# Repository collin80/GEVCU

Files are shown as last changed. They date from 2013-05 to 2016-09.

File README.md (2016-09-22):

GEVCU
=====

Note - If you have pulled this code between July and Sept of 2016 then you received commits that have been
removed from this repo. It has been decided to move development of GEVCU6 code over to the GEVCU6 repo.
If you have the commits from that multi-month window then point your origin to the GEVCU6 repo instead
and everything will still be there and be correct. Sorry for any inconvenience this causes.

Generalized Electric Vehicle Control Unit

Our website can be found at : http://www.gevcu.org

A project to create a fairly Arduino compatible ECU firmware
to interface with various electric vehicle hardware over canbus
(and possibly other comm channels)

The project now builds in the Arduino IDE. So, use it to compile, send the firmware to the Arduino, and monitor serial. It all works very nicely.

The master branch of this project is now switched to support the Due. The master branch is sparsely updated and only when the source tree is in stable shape.

The older Macchina code has been moved to its own branch. This code is now *VERY* old but should work to control a DMOC645.

ArduinoDue branch is more experimental than the master branch and includes the work of Michael Neuweiler.

The WIP branch is sync'd to EVTV's official changes and as such could be considered as a testing ground for the official source code distribution.

You will need the following to have any hope of compiling and running the firmware:
- A GEVCU board. Versions from 2 and up are supported.
- Arduino IDE 1.5.4 - Do not use newer versions of the IDE
- due_can library - There is a repo for this under Collin80
- due_rtc library - Also under Collin80
- due_wire library - once again
- DueTimer library - and again

All libraries belong in %USERPROFILE%\Documents\Arduino\libraries (Windows) or ~/Arduino/libraries (Linux/Mac).
You will need to remove -master or any other postfixes. Your library folders should be named as above.

The canbus is supposed to be terminated on both ends of the bus. If you are testing with a DMOC and GEVCU then you've got two devices, each on opposing ends of the bus. So, both really should be terminated but for really short canbus lines you will probably get away with terminating just one side.

If you are using a custom board then add a terminating resistor. 

If you are using the new prototype shield then it should already be terminated. The DMOC can be terminated by soldering a 120 ohm resistor between the canbus lines. I did this on my DMOC and hid the resistor inside the plug shroud. 

This software is MIT licensed:

Copyright (c) 2014 Collin Kidder, Michael Neuweiler, Charles Galpin, Jack Rickard

Permission is hereby granted, free of charge, to any person obtaining
a copy of this software and associated documentation files (the
"Software"), to deal in the Software without restriction, including
without limitation the rights to use, copy, modify, merge, publish,
distribute, sublicense, and/or sell copies of the Software, and to
permit persons to whom the Software is furnished to do so, subject to
the following conditions:

The above copyright notice and this permission notice shall be included
in all copies or substantial portions of the Software.

THE SOFTWARE IS PROVIDED "AS IS", WITHOUT WARRANTY OF ANY KIND,
EXPRESS OR IMPLIED, INCLUDING BUT NOT LIMITED TO THE WARRANTIES OF
MERCHANTABILITY, FITNESS FOR A PARTICULAR PURPOSE AND NONINFRINGEMENT.
IN NO EVENT SHALL THE AUTHORS OR COPYRIGHT HOLDERS BE LIABLE FOR ANY
CLAIM, DAMAGES OR OTHER LIABILITY, WHETHER IN AN ACTION OF CONTRACT,
TORT OR OTHERWISE, ARISING FROM, OUT OF OR IN CONNECTION WITH THE
SOFTWARE OR THE USE OR OTHER DEALINGS IN THE SOFTWARE.

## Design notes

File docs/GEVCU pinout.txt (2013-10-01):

Pin 1 - +12V Input
Pin 3 - +12V output for first digital input
Pin 7 - EXT GND connection to chassis ground / Battery - (in my case)
Pins 9 & 10 - First canbus
Pin 19 - Gnd connection for first and second analog inputs (Throttle)
Pin 20 - First analog input (Throttle)
Pin 21 - Second analog input (Throttle)
Pin 22 - Third analog input (brake / testing input for me)
Pin 23 - Fourth analog input (test pot on my wires)
Pin 24 - +5V power for first and second analog inputs (Throttle)
Pin 26 - +5V power for third and fourth analog inputs (test pots for me,
probably brake transducer for you)
Pin 30 - Gnd connection for third and fourth analog inputs (Brake / Testing)
Pin 32 - First digital input. Tied to pin 3 above through a switch

I used a gnd at pin 19 for one of the gnds. It really doesn't matter
which one you use. All four (19,29,30,31) are equivalent.

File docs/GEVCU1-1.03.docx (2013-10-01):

GENERALIZED ELECTRIC VEHICLE CONTROL UNIT

GEVCU

SPECIFICATION

Jack Rickard jack@evtv.me

# BACKGROUND

For 40 years and more, individual tinkerers and innovators have been modifying existing automobiles to electric drive and often building electrically powered vehicles from scratch.

The early “controllers” that evolved to replace simple switching and resistive controls to control the speed of the driver motors were mostly pulse width modulated (PWM) devices to provide an averaged DC signal to a series DC motor. These simple chopper voltage control devices were generally referred to as “controllers” and translated driver input from “controls” such as the accelerator pedal, ignition switch, and brake to this motor driving voltage to control its speed and direction – and consequently the vehicle.

There are of course many other types of motors such as separately excited DC motors, brushless DC motors, permanent magnet motors and AC induction motors. Most of these polyphase motors required 3 phase “inverters” to convert the DC power of the battery pack into three phase drive signals varying the voltage and frequency of the power to the motor to accomplish the same thing.

Most of the DC “controllers” received the inputs directly by wiring from the sensors or controls in the cars.

In recent years, among automobile manufacturers, the use of the Controller Area Network bus protocol has been adopted for many of the items in the automobile, including the internal combustion engine – often called an Engine Control Unit or a Vehicle Control Unit which forms the central “brains” of the car. It is connected to various sensors and controls by wire but communicates to other subsystems of the vehicle such as the instrumentation, ABS system, transmission, environmental system using this CANbus as the common link.

Automakers have eschewed the DC motor in favor of either permanent magnet AC motors or AC induction motors. And the “inverters” developed to drive these were interfaced to this same CANbus model for control input.

Because of the varying nature of the cars, the ECU or VCU would be specifically designed for that vehicle. But the Inverters driving AC motors can be somewhat generalized to work in any car by using CANbus to control them.

The VCU would be specifically designed and software specifically written for that vehicle. This was hardcoded into flash memory and defined the operation of the vehicle. No end user input or options were provided. Firmware updates were accomplished by revising the hard code, recompiling, and having the controller reflashed with the new binaries at the dealership during normal maintenance.

And so thousands of these VCUs could be flashed when built, with the software specific to that particular vehicle.

The VCU would of course be completely inappropriate and non functional in another vehicle make or model.

As many automakers are experimenting with product introductions of plug-in electric vehicles and hybrid gasoline/electric vehicles, many of the components used in these vehicles are becoming available when the cars are salvaged and are recycled through salvage yards and such online services as eBay.

As such, they will become a resource to individual tinkerers and those converting existing cars to electric drive.

But almost all of these components were designed to be controlled by the Vehicle Control Unit that came with the original car.

It would be a serious advantage, to have a more generalized vehicle control unit that allowed some basic configuration allowing these conversions to modify operation of the VCU to accommodate THEIR car without the need to entirely rewrite the software and flash the VCU.

As almost all VCU accomplish the same basic functions, a simple configuration input that does not involve assembly language or C programming to change it would be of substantial utility.

This document describes the design of a Generalized Vehicle Control Unit. The multicontroller hardware will allow connection of the basic sensor set necessary to drive the car such as throttle signals, brake signals, ignition signal, and control the basic common outputs such as brake lights, fuel level, rpm, power usage, while serving in the central role of converting these inputs to CAN messages for the inverter to actually drive the car.

The operation of this device can be modified, within fairly narrow constraints, by a simple configuration “menu” style input that non-programmers can access and make changes to, in order to interface the VCU to the particular car they want to convert.

The initial immediate need for this Generalized Vehicle Control Unit was the acquisition of a significant number of Siemens 1PV5135-4WS14-Z motors and Digital Motor Control (DMOC) 645 units from the liquidation of Azure Dynamics Corporation by EVtv.

This DMOC no longer has control inputs, but is rather designed to respond to CANbus commands solely.

The intent in developing this GEVCU, is to not only allow access to a number of OEM hardware components, but also to transfer the product support function faced by the manufacturers and developers of the Inverter Power Electronics to the GEVCU.

In theory, CANbus message digests for ANY motor inverter could be easily patched into the GEVCU to allow operation of that power inverter without ANY support from the developer of the power electronics.

This should quickly allow the developers of power electronics inverters to provide this equipment to individuals at the same or comparable prices as they do to the OEM automakers, without having to incur additional expense to train and support those users in the use of the product. Training and use becomes a function of using the GEVCU itself.

# HARDWARE DESIGN PHILOSOPHY

GEVCU developers can use any hardware they can build or locate that accommodates the basic sensor inputs and instrumentation outputs described in this document. OPEN SOURCE hardware prototype equipment is preferred for GEVCU development and the software should be designed to operate on an open source prototype system. But it is perfectly acceptable to then design custom hardware from that reference design to reduce costs and eliminate extraneous unused components available in the open source prototype system design.

The hardware must provide:

1. At least one CANbus port capable of CAN 1.0 and 2.0b operation, including both 11 bit and 29 bit identifiers.
2. A sufficient number of analog to digital converter inputs of sufficient resolution to accommodate the sensor inputs described in this document. Vehicle sensors are overwhelmingly based on 0-5V architectures. And so these A/D inputs must accept signals in the 0-5v range, and the device must be able to provide 5v supplies to those sensors in sufficient power levels to not alter the 5v reference level when all such sensors are connected.
3. Digital inputs capable of recognizing on/off signals from the vehicle given in 12v and ground states. Active can be either of active high 12v or active low gnd but active high is the normally preferred method as 12v is normally the enabling signal for other systems such as brake lights.
4. Relay driver outputs. Digital outputs suitable for engaging relays, contactors, and other relay like devices in the vehicle.
5. PWM outputs. Sufficient PWM outputs to drive legacy instrumentation such as tachometers and fuel gages as described in this document.
6. ETHERNET port. It is very important for the end user to be able to modify the operation of this device (configure it) without the need for unique external software programs running on specific operating systems. The user should be able to easily configure this device using any device with an Ethernet connection and an http browser. It is actually completely acceptable to also provide means of configuration using a browser via 802.b/g/n wireless, Bluetooth, or Universal Serial Bus (USB) interfaces.

The overall requirement here is that no special type of computer, operation system, or unique configuration software external to the GEVCU can be required to easily modify GEVCU configuration and operation.

Additionally we seek to AVOID the additional expense in the device of a dedicated display and input devices in the GEVCU hardware itself. Once configured, this hardware would be entirely redundant. Configuration is conceivably a one time or perhaps very infrequent event.

7. Processor power sufficient to perform the GEVCU tasks without delay in vehicle operation or control. This is quite important as many systems shut down without regular updated CAN messages to keep them alive and the results of any inability to make schedule could be catastrophic in a moving vehicle.
8. Popularity and user base. When selecting hardware, recognize the advantage of popular and widely adopted devices with large user base. That user base provides a level of additional support and utility that it forms a serious element of the ultimate value of the GEVCU.
9. Tool chain. Strong preference should be given to devices with simple and free compilers such as the Arduino IDE. An open hardware open software device makes little sense if it requires a $2800 compiler environment to make code changes.

# SOFTWARE DESIGN PHILOSOPHY

The basic software design philosophy is to be an open source, object oriented software design. This is to accommodate a couple of needs for the GEVCU

1. Ability to add contributions from any external source or user that prove effective in practice. Anyone should be able to read, modify, recompile and run the original source code to the GEVCU. As such, it should be open source and use inexpensive or free, widely available tool chains to compile. If they are caught in the act of doing something useful, that improvement can be added to the main trunk of the software development.
2. Ability to add support for additional inverters. Almost all of the available inverters accomplish essentially the same functions and provide essentially the same information. But the specific CAN bus IDs, command structure and data formats vary entirely from one inverter to another.

The GEVCU will be initially developed to support the Azure Dynamics DMOC645 inverter. But the ability to add the specific CAN bus message commands for other inverters, without having to make changes to the main program structure in a modular fashion is very important.

Make a strong effort to isolate the inverter object from the rest of the code, with an eye towards allowing the use of other inverter objects with no changes to the non-inverter object code.

3. Object Oriented C++ code is an obvious choice. Assembly language subroutines where desirable or advantageous are perfectly acceptable.
4. Recognize an inevitable desire to add additional functions to this device quite beyond the initial GEVCU spec. The GEVCU, by virtue of it’s central role in vehicle operation, would be the natural place to go for controlling electrically powered air conditioner compressors, CANbus controlled battery chargers, CANbus controlled Electronic Power Assisted Steering units (EPAS) etc.

# COMPLIANCE

For teams developing GEVCU hardware and/or software, it should be noted that compliance with this specification is ENTIRELY voluntary.

That said, there is a slight motivator you might want to take into consideration. I happen to know that software developers are notoriously averse to actually documenting anything and hardware designers are even worse – they not only don’t document but they can’t remember either. They’ll have to get with Charlie and get back to you later.

On the other hand, if you design TO the GEVCU specification, and when making necessary changes NOT in compliance get those changes incorporated BACK into the spec, you will find an odd resemblance between your newly finished product and my upcoming best selling novel :

# INSTALLATION AND OPERATION OF THE GENERALIZED ELECTRIC VEHICLE CONTROL UNIT.

By Jack Rickard.

See the movie at a theatre near you. Coming this summer.

# PART 1 - INPUTS

# THROTTLE

The throttle or accelerator is undoubtedly the central control input for a controller. This is how we vary the power output of the inverter to the motor, and thus motor speed and torque, and consequently vehicle speed.

There are two broad types of throttles that must be accommodated: legacy throttles and modern dual signal drive by wire throttles found in currently manufactured vehicles.

The legacy throttle most widely used is a simple 5kohm potentiometer linked to a mechanical pedal usually by wire. The controller provides 5v and a reference ground to the two ends of the resistor, and the pickup arm of the potentiometer returns some fraction of that source voltage to the controller as the signal input.

There are also single channel hall-effect throttles available on the market. But their operation is largely identical. 5v and ref gnd is provided to them, and they return some value between 0 and 5v based on position.

Modern drive by wire throttles used in vehicles today use the same 5v and ref gnd input, but they will provide TWO signal inputs to the controller. These are often two signals of different scale: ie. 0.5 to 4.5 and 1.2 to 3.2. Or they might be inverse function where one signal is 1-4v while the other is 4-1v. In some cases they can be both differing in scale and direction.

These throttles are generally designed for safety in that the controller is suppose to compare the two signals, which have a known relationship, and if the two signals do not correspond, the assumption is that one or both are faulty. As a result, the controller reduces all motor torque and speed commands to zero. This prevents a runaway situation resulting from loss of ground, or loss of 5v, or other wiring incident or component failure.

PINS: 1. 5vdc supply voltage 50 ma out to sensor

2. Signal 0-5vdc ADC input ADC

3. Optional sanity check voltage ADC input

3. Reference return – ground out to sensor

CONFIGURATION VARIABLES:

THROTMIN: This parameter sets the minimum voltage where the throttle is considered active. Voltages below this value are read as no throttle input.

Example: 0.80 would indicate 0.80v

THROTMAX: This parameter sets the maximum voltage where the throttle is considered active. Voltages above this value are read as no throttle input.

Example: 4.75 would indicate 4.75v

THROTNOTMIN: This parameter sets the minimum voltage where the optional sanity check throttle input is considered active. Voltages below this value are read as no throttle input.

Example: 1.20 would indicate 1.20v

THROTNOTMAX: This parameter sets the maximum voltage where the optional sanity check throttle input is considered active. Voltages above this value are read as no throttle input.

Example: 3.60 would indicate 3.60v

The sanity check is NOT performed if either THROTNOTMIN or THROTNOTMAX is zero. If they are non zero, the percentage of maximum throttle signal between THROTNOTMIN and THROTNOTMAX is calculated. Also the percentage of maximium throttle signal between THROTMIN and THROTMAX is calculated. The two percentages are compared, and if not within 5% of each other, a fault is thrown and CANbus signals generated to put inverter at zero torque and zerospeed.

Note that this calculation MUST handle the case where THROTNOTMIN is a larger positive voltage value than THROTNOTMAX – the inverse case.

THROTREGEN: Voltages between this value and THROTMIN result in a linear increase in regenerative braking, with maximum regenerative braking established by THROTMAXREGEN at the THROTMIN voltage and essentially 0 percent of MAXREGEN at the THROTREGEN point.

Example: 1.50 indicates 1.50v

Zero regenerative braking at 1.50 v increasing to THROTMAXREGEN at THROTMIN.

In this way, as you begin easing off the throttle through the deadband, at THROTREGEN regenerative braking is still zero. As the voltage falls, regenerative braking INCREASES to the point set by THROTMAXREGEN when the voltage falls to THROTMIN. And so the further we remove the throttle, the greater the amount of regenerative torque is applied.

THROTFWD: Typically a small voltage value above THROTREGEN establishing a “dead band” between the THROTREGEN point and the THROTFWD point.

Example: 1.8v

In this example, from THROTREGEN (1.50v_ to THROTFWD (1.8v) is the deadband or coast zone. NO torque or speed commands are provided to the inverter if throttle input is both valid and in this band, allowing the motor and the vehicle to free roll.

The area between THROTFWD and THROTMAX defines the region of forward acceleration with the minimum torque/speed values occurring at THROTFWD and the maximum torque and speed values at THROTMAX.

THROTMAP: This variable represents a voltage between and THROTMAX where a 50% torque and speed level is defined.

A linear increase of torque and speed is mapped between THROTFWD and THROTMAP with 50% of available torque and speed occurring at THROTMAP.

A linear increase in torque and speed is also mapped between THROTMAP and THROT MAX representing the remaining 50% of available torque.

This entered value is then used to warp the throttle curve. For example:

THROTFWD: 1.80v

THROTMAP: 3.80v

THROTMAX: 4.65v

It can be seen that the first 50% of available torque is mapped between 1.80 and 3.80v while the second 50% of available torque is mapped linearly between 3.80v and 4.65v.

In this way, low speed handling and maneuvering has greater resolution spread across 2.00v of the throttle range, while less resolution is provided across the upper 0.85v. Higher resolution is desired at take off, or while parking, or reversing, while it is generally not needed in going from 50% to full power when we are basically just wanting a big increase in power. THROTMAP can be used to slide this point between those two extremes.

THROTMAXREGEN: This variable defines the percentage of available maximum torque that is available for regenerative braking at the THROTMIN point.

Note that a value of 0 indicates no regenerative braking at all using the throttle.

MAXREGEN: This variable defines the percentage of available maximum torque that is ever available for regenerative braking.

MAXTORQ: This defines the maximum torque available for any purpose.

# BRAKE

You might note that the throttle input also has provisions for regenerative braking. The brake signal does as well. We would assume that the vehicle has a fully functional normal brake system, and that it also has a brake switch used to turn on the brake lights.

Regenerative braking is normally a function of the brake input.

PINS: 1. 5vdc supply voltage 50 ma out to sensor

2. Brake pressure sensor signal 0-5vdc input ADC

3. Reference return – ground out to sensor

4. Brake light input – 0 or 12v digital input

CONFIGURATION VARIABLES:

BRAKEMIN: This parameter sets the minimum voltage where the brake sensor is considered active. Voltages below this value are read as no brake input.

BRAKEMAX: The maximum voltage logic will read as valid brake pressure sensor input. Voltages above BRAKEMAX are read as no brake input.

BRAKEMAXREGEN. This is a value from 0 to 100 representing the percentage of MAXTORQ that can be applied during regenerative braking.

The actual value of regenerative braking during a braking event is a linear value between MAXTHROTREGEN at BRAKEMIN and BRAKEMAXREGEN at BRAKE MAX.

In this way, when you remove your foot from the throttle, the regenerative level is set at the value of MAXTHROTREGEN. When your foot first applies to the brake, that SAME level of REGEN is maintained. As more brake pressure is applied, the regenerative braking torque increases until it reaches BRAKEMAXREGEN at the BRAKEMAX point.

Note that by setting BRAKEMAX to some voltage LESS than the actual maximum voltage provided by the sensor, you can slide the regenerative braking zone toward the very lightest application of brake, and as you continue to press the pedal, regenerative braking ceases and the normal brake system takes over. This can be effective to get maxium regenerative braking effect before the normal disk or drum brakes begin to become effective.

Normally, NO regenerative braking will be provided without a secondary signal from the brake light input. This is a secondary input from a separate source used to enable regenerative braking.

BRAKREGENRAMPTIME. This is a value between 0 and 255 representing the number of hundredths of a second to use to ramp from THROTMAXREGEN to BRAKEMAXREGEN if the brake sensor input value is below BRAKEMIN but the brake light input is active.

In this event, we assume we are NOT USING a brake pressure tranducer input at all. But we do have an active brake light switch signal. The regenerative braking will gradually increase from THROTMAXREGEN to BRAKEMAXREGEN in linear fashion across the entered time value with a max time of 2.5seconds.

This is counterintuitive and we’ve actually seen inverters with this function coded in backwards. But it doesn’t work well when braking.

In the event we are not using regen on the throttle, and want to use it on the brakes, but have no transducer, the regenerative braking will gradually be applied when we step on the brake pedal and steadily increase. If we get too much braking, we simply remove our foot from the brake. Regen goes to zero. We can REAPPLY the brake pedal and again regenerative braking starts to increase. In practice, this feels like you are pumping the brakes.

# REGENERATIVE BRAKING ADJUST

Regenerative braking is a highly subjective “feel” issue. It would be very nice to provide a knob on an electric vehicle where the driver could manually adjust the regen level just by turning the knob.

PINS: 1. 5vdc supply voltage 50 ma out to sensor

2. Regenerative brake adjust signal 0-5vdc input ADC

3. Reference return – ground out to sensor

CONFIGURATION VARIABLES:

REGENSCALE. This variable is set between 0 and 100% based on the voltage read on the regenerative braking adjust signal input. Voltages below 1v set this value to 0. Voltages between 1 and 4v are converted to a decimal value less than 1 indicating the percentage of regen desired. Voltages above 4 are read as 4.

THROTMAXREGEN and BRAKEMAXREGEN are scaled by multiplying the values entered on the configuration screen by REGENSCALE.

As a result, potentiometer settings resulting in an input voltage less than 1 effectively disables regenerative braking. Voltages between 1 and 5 scale regenerative braking.

# IGNITION

The switched ignition 12v from the vehicle is used to turn on the GEVCU. It is also the source of power for the GEVCU.

PINS: 1. 12vdc supply voltage in from vehicle ignition switch.

CONFIGURATION VARIABLES: None.

# FORWARD

The internal DIRECTION variable should be used to indicate forward (1), reverse (2), or neutral (0) operation. IF REVERSE and NEUTRAL input pins are inactive, set DIRECTION to 1.

PINS: 1. 12vdc digital input.

CONFIGURATION VARIABLES:

ACTIVEHIGH. This single configuration variable determines if input pins are active high (greater than 4 volts) or active low (less than 3 volts). All digital input pins should be able to endure voltage values up to 15v which may occur in vehicles. This variable applies to ALL digital input pins on the VCU.

# REVERSE

The internal DIRECTION variable should be used to indicate forward (1), reverse (2), or neutral (0) operation. IF FORWARD and NEUTRAL input pins are inactive, set DIRECTION to 2.

PINS: 1. 12vdc digital input.

CONFIGURATION VARIABLES:

ACTIVEHIGH. This single configuration variable determines if input pins are active high (greater than 4 volts) or active low (less than 3 volts). All digital input pins should be able to endure voltage values up to 15v which may occur in vehicles. This variable applies to ALL digital input pins on the VCU.

# NEUTRAL

The internal DIRECTION variable should be used to indicate forward (1), reverse (2), or neutral (0) operation. IF FORWARD and REVERSE input pins are inactive, set DIRECTION to 0.

PINS: 1. 12vdc digital input.

CONFIGURATION VARIABLES:

ACTIVEHIGH. This single configuration variable determines if input pins are active high (greater than 4 volts) or active low (less than 3 volts). All digital input pins should be able to endure voltage values up to 15v which may occur in vehicles. This variable applies to ALL digital input pins on the VCU.

# GENERAL ENABLE

This input can be used to enable the VCU operation. If active, AND the GENERAL DISABLE input is INACTIVE, sets internal variable ENABLE to 1. This internal variable is used to determine whether to allow drive speed and torque commands to the inverter. If this input goes inactive, the ENABLE variable is set to 0.

PINS: 1. 12vdc digital input.

CONFIGURATION VARIABLES:

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

# GENERAL DISABLE

This input can be used to enable the VCU operation. If any of these three input pins go active, sets internal variable ENABLE to 0 regardless of GENERAL ENABLE input. This internal variable is used to determine whether to allow drive speed and torque commands to the inverter. If this input goes inactive, NO change is made to the ENABLE variable and we rely on the general enable input to reset ENABLE to 1.

PINS: 1. 12vdc digital input – DISABLE 1.

2. 12vdc digital input - DISABLE 2

3. 12vdc digital input - DISABLE 3

CONFIGURATION VARIABLES:

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

# LIMP MODE

This input is used to force an immediate reduction in power available via speed and torque command. All speed and torque commands are scaled by the LIMPSCALE variable.

PINS: 1. 12vdc digital input.

CONFIGURATION VARIABLES:

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

LIMPSCALE. 0-100. This configuration variable is used as a multiplier for ALL torque and speed commands to the vehicle. The default value is 100 indicating full power Scotty. Lower values of course reduce output power to the percentage indicated in this variable. The variable is applied ONLY when the LIMPMODE input is active.

# OUTPUTS

# CONTROLLER STATUS

This output is used to indicate status of the GEVCU. If it is turned ON and left on in a steady state, this indicates the GEVCU has powered up, established communications with the inverter, and passed all internal operational checks.

PINS: 1. Digital output LED driver.

CONFIGURATION VARIABLES: None

If this LED is flashed 1 to 9 times, followed by off for two seconds, followed by another series of flashes 1 to 9, this indicates a fault code. Fault codes can be, 11 through 19, 21 through 29, 31 through 39 etc. up to 99.

Fault Code 99 is defined as FAULT - NO FAULT CODE PROVIDED.

Fault Code 11 is defined as NO INVERTER COMMUNICATIONS.

Any developer can register a fault code and we’ll add it. First come, first served.

# PRECHARGE RELAY OUTPUT

This output is used to close a precharge relay, applying high voltage to the Inverter through a precharge resistor. icates the GEVCU has powered up, established communications with the inverter, and passed all internal operational checks.

PINS: 1. Digital output 12v RELAY driver. 500ma

CONFIGURATION VARIABLES:

PRECHARGERELAY: This variable is set by the user using a checkbox or radio button. The variable is set to 1 if selected and 0 if not indicating the need for a precharge relay output on power up.

If 1, a digital output is provided as part of the startup sequence. If the digital output does not provide sufficient current, an external MOSFET may be required to drive the relay.

Many inverters such as Rinehart do their own precharge management. The DMOC 645 does not. So this will always be an optional output configurable by the user.

# CONTACTOR RELAY OUTPUT

This output is used to close a contactor high current relay, applying high voltage to the Inverter directly. Most contactors can experience an initial closing current requirement of up to 1.5 amps and subsequently settle to 300 ma or so.

PINS: 1. Digital output 12v RELAY driver. 1.5 amps.

CONFIGURATION VARIABLES:

CONTACTOR: This variable is set by the user using a checkbox or radio button. The variable is set to 1 if selected and 0 if not indicating the need for a contactor relay output on power up.

If 1, a digital output is provided as part of the startup 3 seconds after the PRECHARGERELAY output. If the digital output does not provide sufficient current, an external MOSFET may be required to drive the contactor.

# REVERSE LIGHT RELAY OUTPUT

This output is used to close a relay, applying 12v to the reverse lights of the vehicle. This will normally be done by the transmission, but on certain vehicles without transmission, could be reversed using the REVERSE input to reverse the motor speed and torque commands. This output is always available and set active whenever the internal DIRECTION variable is set to 0

PINS: 1. Digital output 12v RELAY driver. 500 ma.

CONFIGURATION VARIABLES: None

If the digital output does not provide sufficient current, an external MOSFET may be required to drive the 12v relay

# COOLING RELAY OUTPUT

This output is used to close a relay, applying 12v to drive cooling pumps or fans or both. This is set to active whenever CANbus status signals are received from the inverter indicating a motor or inverter temperature reaching a certain level.

PINS: 1. Digital output 12v RELAY driver. 500 ma.

CONFIGURATION VARIABLES:

COOLINGTEMP: 0-300

This configuration variable allows the user to enter the temperature of either motor or inverter where the coolant output goes active. Zero to 300C.

# MOTOR TEMPERATURE OUTPUT

This is a Pulse Width Modulated output representing motor temperature. It can be used to drive a temperature gage. It will be active only if motor temperature is available from inverter via CAN status message.

PINS: 1. 5v PWM output.

CONFIGURATION VARIABLES:

MOTORMINTEMP: 0-300

This variable allows user to enter a motor temperature corresponding to the lowest reading on their gage and nominally a PWM value of 0%.

MOTORMAXTEMP: 0-300

This variable allows the user to enter a motor temperature in degrees centigrade to correspond with a PWM output of 100%.

# INVERTER TEMPERATURE OUTPUT

This is a Pulse Width Modulated output representing inverter temperature. It can be used to drive a temperature gage. It will be active only if inverter temperature is available from inverter via CAN status message.

PINS: 1. 5v PWM output.

CONFIGURATION VARIABLES:

INVMINTEMP: 0-300

This variable allows user to enter an inverter temperature corresponding to a PWM value of 0%.

INVMAXTEMP: 0-300

This variable allows the user to enter an inverter temperature in degrees centigrade to correspond with a PWM output of 100%.

Output should of course be scaled from INVMINTEMP to INVMAXTEMP 0 to 100%. Temperatures above max will be shown at 100% and temperatures below min will be shown at 0% but of course.

# RPM OUTPUT

This is a pulsed digital output that can be used with a 12v opto isolator to drive a common tachometer. RPM from Inverter CAN status message is converted to a series of digital pulses..

PINS: 1. pulsed digital output.

CONFIGURATION VARIABLES:

TACHPPT:

This variable allows user to enter the number of pulses to output per turn PPT corresponding to their tachometer. The output is scaled to a frequency representing this number of pulses per rpm.

Example: 6000 rpm = 100 rps x 4ppt = 400Hz

# BATTERY CURRENT OUTPUT

This is a pulsed digital output that can be used with a 12v opto isolator to drive a common tachometer. Battery current from Inverter CAN status message is converted to a series of digital pulses..

PINS: 1. pulsed digital output.

CONFIGURATION VARIABLES:

AMPPPT:

This variable allows user to enter the number of pulses to output per turn PPT corresponding to their tachometer. The output is scaled to a frequency representing this number of pulses per rpm.

Example: 600 amp = 100 rps x 4ppt = 400Hz

In this case 600 amps of battery current will appear on a tachometer as 6000 rpm if it is a 4 pulse per turn tachometer.

# OTHER CONFIGURATION VARIABLES

MAX RPM – maximum RPM controller should command to inverter.

MAX TORQUE – maximum torque controller should command to inverter.

MAX REGEN – maximum regenerative braking torque controller should command.

# GEVCU STATUS DISPLAY HTML

### Battery voltage _____v

### Battery current ______A

### Battery power ______kW

### Motor temp: ______C

### Inverter temp: ______ C

### Motor Torque: ______ %

### Motor Speed: ______rpm

### Power used since start: _____kWh

### BUTTON – GEVCU SETUP

# GEVCU CONFIGURATION

# GENERAL LIMITS

### MAXRPM (1000-10000) ______rpm

### MAXTORQUE (0-100): ______%

### ACTIVEHIGH [ ] yes [ ] no

### LIMPSCALE(0-100) ____%

# THROTTLE/ACCELERATOR

### THROTMIN (0.00-5.00v) : _________v

### THROTREGEN (0.00-5.00): _______v

### THROTFWD(0.00-5.00): _______v

### THROTMAP(0.00-5.00): _______v

### THROTMAX(0.00-5.00): _______v

### THROTNOTMIN(0.00-5.00): _______v

### THROTNOTMAX(0.00-5.00): _______v

### 0.00==THROTMIN==THROTREGEN==THROTFWD==THROTMAP=THROTMAX ==5.00

### 0.00==THROTNOTMIN=============================THROTNOTMAX-====5.00

\

# BRAKE INPUT

### BRAKEMIN (0.00-5.00v) : _________v

### BRAKEMAX (0.00-5.00): _______v

# REGENERATIVE BRAKING

### MAXREGEN (0-100): _____%

### REGENSCALE (0-100): _____%

### THROTMAXREGEN (0-100) ____%

### BRAKEMAXREGEN (0-100) ____%

### BRAKEREGENRAMPTIME(0-255): _______seconds

# OUTPUTS

### PRECHARGE RELAY OUTPUT [ ] yes [ ] no

### CONTACTOR OUTPUT [ ] yes [ ] no

### COOLING OUTPUT(0-300): _______centigrade

### MOTORMINTEMP(0-300): _______centigrade

### MOTORMAXTEMP(0-300): _______centigrade

### INVERTERMINTEMP(0-300): _______centigrade

### INVERTERMAXTEMP(0-300): _______centigrade

### TACHPPT (0-8) ____ ppt

### AMPPPT (0-8) ____ ppt

### BUTTON – ACCEPT CONFIG CHANGES

### BUTTON – GEVCU STATUS

# GEVCU CONFIGURATION TOOLTIPS

Tooltips that may be incorporated into GEVCU configuration html form.

# GENERAL LIMITS

### MAXRPM (1000-10000) ______rpm

The maximum motor speed the GEVCU will call for or allow. If this limit is reported by the Inverter, motor torque, speed or both will be reduced by CANbus command.

### MAXTORQUE (0-100): ______%

The maximum motor torque that can be commanded by CANbus

### ACTIVEHIGH [ ] yes [ ] no

Yes indicates activation of digital inputs will be read with 12v applied to pin. No indicates ACTIVE LOW with ground applied to pin read as ACTIVE.

### LIMPSCALE(0-100) ____%

Percent of maximum torque and speed allowed when LIMPMODE input is active.

# THROTTLE/ACCELERATOR

### THROTMIN (0.00-5.00v) : _________v

Values below this voltage are read as a fault on the accelerator input.

### THROTREGEN (0.00-5.00): _______v

Regenerative braking is linearly increased from this voltage/pedal position DOWN to THROTMIN.

### THROTFWD(0.00-5.00): _______v

Region between THROTREGEN and THROTFORWD defines dead band or COAST area of throttle. Torque and speed are linearly increased from this point to THROTMAX.

### THROTMAP(0.00-5.00): _______v

Defines point between THROTFWD and THROTMAX where 50% of available torque/speed is available. By setting this higher, better low speed resolution/control.

### THROTMAX(0.00-5.00): _______v

Voltages above this are read as throttle faults.

### THROTNOTMIN(0.00-5.00): _______v

Minimum voltage of second throttle input. 0 indicates no input. Any other value establishes ratio to THROTMIN

### THROTNOTMAX(0.00-5.00): _______v

Maximum voltage of second throttle input. 0 disables second throttle input. Any other value corresponds to THROTMAX. It is acceptable for THROTNOTMIN to be greater than THROTNOTMAX, indicating a reversed linear input for comparison to the main throttle input.

### 0.00==THROTMIN==THROTREGEN==THROTFWD==THROTMAP=THROTMAX ==5.00

### 0.00==THROTNOTMIN=============================THROTNOTMAX-====5.00

\

# BRAKE INPUT

### BRAKEMIN (0.00-5.00v) : _________v

Voltages below BRAKEMIN are read as brake sensor faults. Regenerative braking is linearly ramped between BRAKEMIN and BRAKEMAX in most instances.

### BRAKEMAX (0.00-5.00): _______v

Voltages above BRAKEMAX are read as brake sensor faults. Regenerative braking is linearly ramped between BRAKEMIN and BRAKEMAX in most instances.

# REGENERATIVE BRAKING

### MAXREGEN (0-100): _____%

Percentage of MAXTORQUE that can be applied as regenerative braking.

### REGENSCALE (0-100): _____%

MAXREGEN, THROTMAXREGEN, and BRAKEMAXREGEN are all reduced identically if this value is less than 100.

### BRAKEMAXREGEN (0-100) ____%a

Percent of MAXREGEN allowed for braking

### BRAKEREGENRAMPTIME(0-255): _______seconds

Number of seconds to ramp from THROTTREGEN to BRAKEMAXREGEN in the event there is no brake pressure sensor input and we are doing regenerative braking from the brake light input only.

# OUTPUTS

### PRECHARGE RELAY OUTPUT [ ] yes [ ] no

Yes if you want a relay drive signal to engage an external relay. No if not.

### CONTACTOR OUTPUT [ ] yes [ ] no

Yes if you want a 1.5amp relay output to engage high voltage contactor relay

### COOLING OUTPUT(0-300): _______centigrade

Temperature of motor or inverter where a COOLING relay output is provided.

### MOTORMINTEMP(0-300): _______centigrade

Minimum motor temperature corresponding to 1% PWM output on MOTOR TEMP output.

### MOTORMAXTEMP(0-300): _______centigrade

Motor temperature corresponding to 99% PWM output on MOTOR TEMP .

### INVERTERMINTEMP(0-300): _______centigrade

Minimum reported inverter temperature corresponding to 1% PWM output on INVERTER TEMP output.

### INVERTERMAXTEMP(0-300): _______centigrade

Inverter temperature corresponding to 99% PWM output on INVERTER TEMP .

### TACHPPT (0-8) ____ ppt

Pulses per turn for dashboard tachometer to read RPM output of GEVCU

### AMPPPT (0-8) ____ ppt

Pulses per turn for dashboard tachometer to read amperes in hundreds on tachometer thousands of RPM gage.

### BUTTON – ACCEPT CONFIG CHANGES

Sends these configuration changes to GEVCU

### BUTTON – STATUS

Causes GEVCU to display current status screen.

# GEVCU EEPROM MAPPING

This section describes the mapping and location of certain configuration variables necessary for the Generalized Vehicle Control Unit. When an end user sends the HTML form containing configuration items, those items will be extracted from the HTML and stored in the Macchina EEPROM so they are persistent between operations. The program can then retrieve these configuration variabales from EEPROM as part of the basic initialization procedure.

1000 unsigned int MAXRPM (1000-10000) ______rpm

1002 byte MAXTORQUE (0-100): ______%

1003 bool ACTIVEHIGH [ ] yes [ ] no

1004 byte LIMPSCALE(0-100) ____%

1005 unsigned int THROTMIN (0-500 /0.00-5.00v) : _________v

1007 unsigned int THROTREGEN 0-500(0.00-5.00): _______v

1009 unsigned int THROTFWD 0-500(0.00-5.00): _______v

1011 unsigned int THROTMAP 0-500(0.00-5.00): _______v

1013 unsigned int THROTMAX 0-500 (0.00-5.00): _______v

1015 unsigned int THROTNOTMIN 0-500(0.00-5.00): _______v

1017 unsigned int THROTNOTMAX0-500(0.00-5.00): _______v

1019 unsigned int BRAKEMIN 0-500(0.00-5.00v) : _________v

1021 unsigned int BRAKEMAX 0-500(0.00-5.00): _______v

1023 byte MAXREGEN (0-100): _____%

1024 byte REGENSCALE (0-100): _____%

1025 byte THROTMAXREGEN (0-100) ____%

1026 byte BRAKEMAXREGEN (0-100) ____%

1027 byte BRAKEREGENRAMPTIME(0-255): _______seconds

1028 bool PRECHARGE RELAY OUTPUT [ ] yes [ ] no

1029 bool CONTACTOR OUTPUT [ ] yes [ ] no

1030 unsigned int COOLING OUTPUT(0-300): _______centigrade

1032 unsigned int MOTORMINTEMP(0-300): _______centigrade

1034 unsigned int MOTORMAXTEMP(0-300): _______centigrade

1036 unsigned int INVERTERMINTEMP(0-300): _______centigrade

1038 unsigned int INVERTERMAXTEMP(0-300): _______centigrade

1040 byte TACHPPT (0-8) ____ ppt

1041 byte AMPPPT (0-8) ____ ppt

GEVCU Specification 1.03 February 7, 2013

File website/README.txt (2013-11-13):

The GEVCU uses the Mini Socket iWifi module from ConnectOne. Documentation can be found at

http://www.connectone.com/?page_id=217

To update the website on the iChip, you have to use their packing tool which is part of their iChipConfig utility and only runs on Windows XP.  If you use Windows 7 you can use Windows XP mode:

http://windows.microsoft.com/en-us/windows7/install-and-use-windows-xp-mode-in-windows-7

Download and install the following:

http://www.connectone.com/wp-content/uploads/2012/06/iChipConfigExternal_2.4.95_setup7.zip

Then to update the website after changes,

1. Launch iChipConfig, click through warnings about not having the com port and limited functionality
2. Choose the "Site Pack" tool
3. Browse to the website/src dir, select the index.htm as default
4. Select "C02128" as the platform and click "Pack". At this point the parameters should show.
5. Select all the parameters, enter 20 for the max length value to fill and click "Fill"
6. Click "Save" and point it to website.img

At this point you upload the image to the GEVCU using http://192.168.3.10/ichip and power cycle the GEVCU to have it activated.

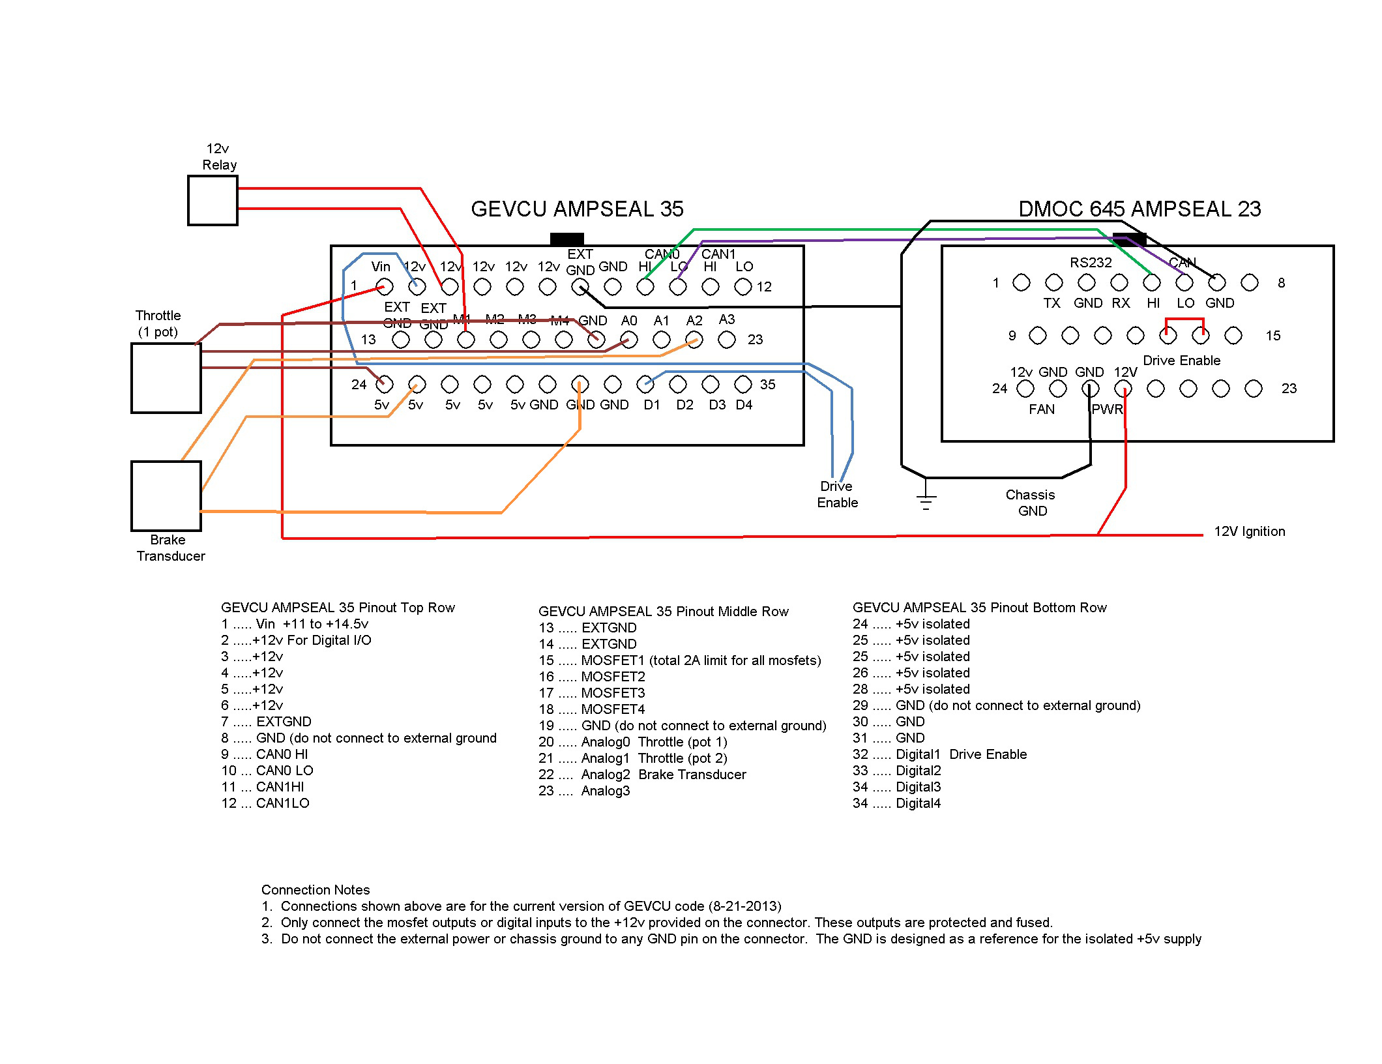
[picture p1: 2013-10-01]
docs/GEVCU-35pinout.jpg

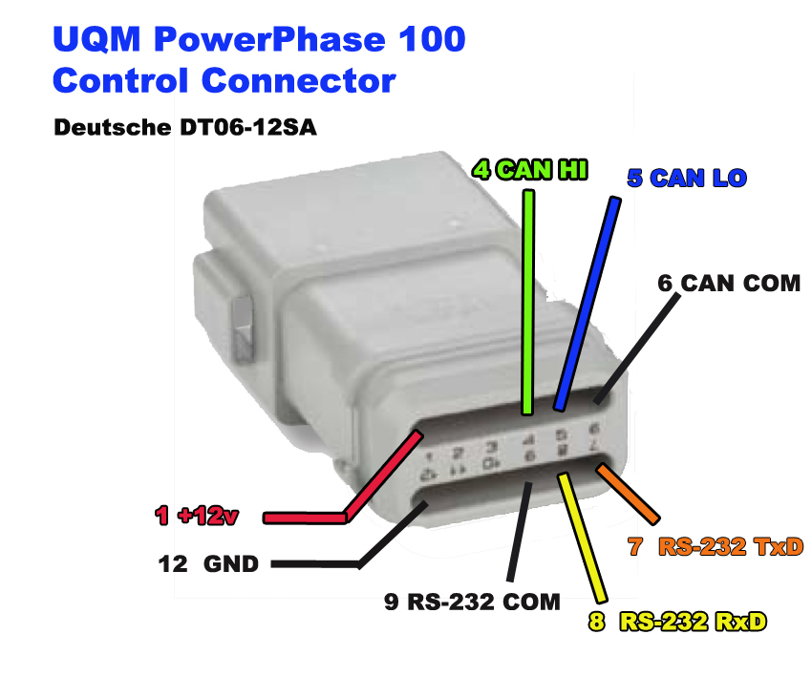
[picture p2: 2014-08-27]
docs/UQMplug.jpg

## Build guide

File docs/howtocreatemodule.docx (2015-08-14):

# GEVCU

Generalized Electric Vehicle Control Unit

# Programmer Checklist

# For Adding Object Modules to the

# GEVCU Software

The Generalized Electric Vehicle Control Unit software is open source and object oriented. It was originally developed to control the Azure Dynamics model 645 Digital Motor Controller (DMOC) – a 3-phase inverter/controller used with the Siemens 1PV5134 motor on the Azure Dynamics eTransit Connect.

The DMOC645 was CAN controlled and did not feature any inputs for throttle, brake or other inputs and outputs. The eTransit Connect Vehicle Control Unit (VCU) performed that duty. Lacking the VCU, we had to develop a VCU from scratch capable of providing the necessary CAN messages to the DMOC645 to in turn control the motor.

The concept of a GENERALIZED VCU specifically for electric vehicles derived from the many different types of cars that would be converted to electric drive using this drive system. But from the beginning we saw the need to drive other types of controller/inverters and indeed interact with other devices such as chargers, DC-DC converters, and battery management systems.

So a central tenet of the GEVCU was a very object oriented approach that would easily allow the addition of new classes and new objects to accommodate different equipment. The goal of course to limit software changes to just the additional object added to accommodate the new equipment.

Some wins and some losses. Indeed GEVCU now supports the BRUSA drive train, the CODA/UQM drive train, and more are envisioned and already a series of chargers, BMS, and other devices have been added.

But along the way, we encountered several targets of opportunity that were just two good to pass on, that tend to complicate the easy addition of object modules.

CREATE OBJECT MODULE

TASKING AND PRIORITIES.

PERSISTENT CONFIGURATION STORAGE

MULTIPLE DEVICES ON CAN

# CREATING AN OBJECT MODULE

You create an object module basically by adding a .cpp and .h file to the program set defining your object module. The best way is to copy one from a similar device. If you are doing an object module for a motor controller, a good start would be to copy and rename the DMOC645 motor controller object module held in DmocMotorController.cpp and DmocMotorController.h

Let’s call the new module EVIC and we’ll rename the copied files EVIC.cpp and EVIC.h.

To add these to the program, you basically do two things.

1. Add an include for EVIC.h in the GEVCU.h header file.

#include "EVIC.h"

2. Add a createObjects entry in the main program file GEVCU.ino

void createObjects() {

PotThrottle *paccelerator = new PotThrottle();

CanThrottle *caccelerator = new CanThrottle();

PotBrake *pbrake = new PotBrake();

CanBrake *cbrake = new CanBrake();

DmocMotorController *dmotorController = new DmocMotorController();

CodaMotorController *cmotorController = new CodaMotorController();

DCDCController *dcdcController = new DCDCController();

BrusaMotorController *bmotorController = new BrusaMotorController();

ThinkBatteryManager *BMS = new ThinkBatteryManager();

ELM327Emu *emu = new ELM327Emu();

ICHIPWIFI *iChip = new ICHIPWIFI();

EVIC *eVIC = new EVIC();}

Here, we instantiated the object eVIC of type EVIC as a new instance of EVIC().

Our eVIC object is now part of the program and enjoys all the rights and privileges of other objects of the program.

Note that most objects you will create will actually be child objects of more generalized parent objects. A motor controller object, for example, usually inherits from MotorController and from CanHandler. Much of the basic work common to all motor controllers is already done for you in the parent and standard variables are already there for you to update from your own specific code. You also generally must inherit from CanHandler to be able to catch and send CAN messages in your object.

So you will find something like this in your .h file.

class EVIC: public Device, CanObserver {

public:

Here, in EVIC.h, we are defining a new class EVIC which inherits from the generic Device class but also from CanObserver. A motor controller might be better to inherit from MotorController and CanObserver.

Obviously, you will likely have to rename almost all the class references in your .cpp and .h files.

# TASKING AND PRIORITIES

We hesitate to claim we have duplicated Linux and a real time operating system here. But the Arduino Due does sport an interesting set of clocks – 3 of them actually – each with 3 configurable interrupt timers for a total of 9 timer interrupts.

Inverter/controllers are operating powerful motors in real time and can be a bit demanding in that they want constant attention – regularly updated CAN control messages or they tend to shut down as a safety consideration. So inverters need the highest priority.

GEVCU does provide information to the user and allows configuration either by USB serial port or via a wireless web site. But while driving down the road, it would be quite normal for NO ONE to be using this at all to configure the system. So this is an example of a very low priority. Chargers and Battery Monitors and so forth would fall somewhere in between.

So we have developed a module called a TICK HANDLER. Your object module must register with this TICK HANDLER and then provide a public method, also termed TICKHANDLER to perform its duties as it can when the TICKHANDLER passes it a tick (timeslice).

You can think of your tickhandler as the LOOP routine in the Arduino Sketch/Processing environment or more traditionally MAIN.

To register your object with the tickhandler, the following general steps are in order.

1. Add a tickhandler DEFINE for your object to config.h file to set your tick interval in microseconds.

#define CFG_TICK_INTERVAL_EVIC 100000

Here, we define a tick interval for EVIC to call it every 100,000 microseconds (100 milliseconds)

2. Add a setup function to your object module establishing tickhandler

void EVIC::setup()

{

TickHandler::getInstance()->detach(this);//Turn off tickhandler

(Any number of other setup statements)

TickHandler::getInstance()->attach(this, , CFG_TICK_INTERVAL_EVIC);

}

In case our tickhandler is on, we turn it off. Perform any other setup functions desired. And then attach the tickhandler using the DEFINE from config.h.

3. Add a tickhandler function to your object module

void EVIC::handleTick()

{

sendCmdCurtis();

sendCmdOrion();

}

Here, we have a short function that calls two other functions. Each of those create and send a CAN command. So each 100 ms, the tickhandler will call the object function handleTick, which will send two CAN messages and return.

4. In your object module .h file, add the following includes:

#include "config.h"

#include "TickHandler.h"

# PERSISTENT CONFIGURATION STORAGE

Almost all modules in the GEVCU have some level of need to store information between operating sessions. This may be system data that you want to maintain from startup to startup such as accumulated Ampere-Hours or peak temperatures.

But almost all devices have some configuration options that end users can adjust to modify the operation of the software.

The Arduino Due ARM3 processor gives us very good power and speed for the VCU function, but it does not provide an EEPROM and the use of flash memory for persistent data has a problem in that it is totally erased if the software is updated.

So GEVCU has a 2Megabit (256kbytes) EEPROM provided just for such persistent data.

In coding independent objects that could be enabled in a variety of combinations, we have to have some means of rationalizing who stores what at what address and when. Otherwise, objects would be overwriting each other’s data.

Further, EEPROM’s have a defined write life. Not quite the issue it was originally, it is still nice to limit the number of writes so that the same data is not rewritten every 30 msec.

We do this with a device termed a MEMCACHE. An object has to register with DEVICES and is allocated a block of memory in MEMCACHE. The data in MEMCACHE is then recorded to EEPROM periodically. And it is loaded into MEMCACHE on startup. In this way, you can save your configuration data and load it again on the next startup.

1. Each device should create a configuration class that inherits from DeviceConfiguration. This will be in your .h file.

class EVICConfiguration: public DeviceConfiguration {

public:

};

2. The loadConfiguration() and saveConfiguration() methods of DmocMotorController and MotorController can be used as a reference for how to load and save configurations.
3. PrefHandler handles the memcache for various devices. Each device needs its own unique name and id number. These are held in the file DeviceTypes.h

enum DeviceId { //unique device ID for every piece of hardware possible

DMOC645 = 0x1000,

BRUSA_DMC5 = 0x1001,

CODAUQM = 0x1002,

BRUSACHARGE = 0x1010,

TCCHCHARGE = 0x1011,

LEAR=0x1012,

THROTTLE = 0x1030,

POTACCELPEDAL = 0x1031,

POTBRAKEPEDAL = 0x1032,

CANACCELPEDAL = 0x1033,

CANBRAKEPEDAL = 0x1034,

EVICTUS = 0x4400,

ICHIP2128 = 0x1040,

DCDC = 0x1050,

THINKBMS = 0x2000,

SYSTEM = 0x5000,

HEARTBEAT = 0x5001,

MEMCACHE = 0x5002,

PIDLISTENER = 0x6000,

ELM327EMU = 0x650,

INVALID = 0xFFFF

};

Here, for the EVIC class we call the device EVICTUS and assign the number 0x4400 to it.

In our object file EVIC.cpp, we have to alter our device constructor to include this.

EVIC::EVIC() : Device()

{

prefsHandler = new PrefHandler(EVICTUS);

commonName = "Andromeda Interfaces EVIC Display";

}

This registers us for the PrefsHandler to provide memcache space. We can then use LoadConfiguration and SaveConfiguration to handle our persistent data that we want to use from session to session without loss.

# MULTIPLE DEVICES ON CAN

GEVCU provides two independent CAN ports that can be configured for different speeds and operated more or less simultaneously. The nature of CAN is that a variety of hardware devices can be on the bus simultaneously as long as they all use the same data speed. And so of course a variety of object modules is envisioned, each servicing one or more CAN devices.

Again to accommodate this without chaos, we have developed a CAN handler. The CAN handler monitors the two CAN busses and when a CAN message is received, the message is passed to the appropriate module. And so each module performing CAN tasks must be registered with the CAN handler as to which specific CAN message IDs it wants to receive.

A canbus handler allows your device to register to receive frames that match the mask. The call to attach has four parameters. The first will basically always be “this”. The second is the ID to match, the third is the mask, and the fourth specifies whether you are interested in standard (false) or extended (true) frames.

canHandlerEv->attach(this, 0x230, 0x7f0, false);

canHandlerCar->attach(this, 0x650, 0x7f0, false);

In this case, we are registering with CAN bus 0 (Ev) to receive any message with an id between 0x230 and 0x23F.

We are also registering with CAN bus 1 (Car) to receive any CAN message with ID 0x650 through 0x65F.

If you need a quick refresher on masks and IDs: CAN bus filtering happens by taking every incoming frame and doing a bitwise AND with each registered mask in turn. The result of this is then compared to the associated ID for that mask. If the two match then your device will receive that frame. For instance, if a frame with 0x23D were to come in and the DmocMotorController had registered a mask of 0x7F0 and an ID of 0x230. 0x23D AND 0x7F0 = 0x230. This does match the ID and so DmocMotorController would get the frame.

Your class should have a handleCanFrame() method if you have registered one or more canbus handlers. This method takes a pointer to a CAN_FRAME structure as input.

# void DmocMotorController::handleCanFrame(CAN_FRAME *frame)

{

}

To send a frame, first create a CAN_FRAME structure variable, fill it out, and use sendFrame() to send it.

### CAN_FRAME output; //establishes variable output of structure CAN_FRAME

### output.length = 8; //Sets number of bytes in payload

### output.id = 0x207; //Sets message id

### output.extended = 0; //0 standard 11 bit frame 1 for extended 29bit frame

### output.data.bytes[0] = 0xa5; //This is simply puts value 5A

### output.data.bytes[1] = 0xa5; //in the first three payload bytes

### output.data.bytes[2] = 0x5a;

### output.data.bytes[3] = 0x00;

### output.data.bytes[4] = 0x00;

### output.data.bytes[5] = 0x00;

### output.data.bytes[6] = 0x00;

### output.data.bytes[7] = 0x00;

### CanHandler::getInstanceEV()->sendFrame(output); //Send the frame

IN this case we establish the variable output as type CAN_FRAME

We set the length to 8 bytes and the message ID to 0x207. We set it for standard 11bit frames and then populate the eight bytes with whatever we like. Then call the can handler to send frame OUTPUT. On the EV (CAN0) bus.

So note that we used a call to the can handler to register our ids and masks for incoming messages, and provided a method to handle those incoming messages by the specific name handleCanFrame.

We used another call to the canhandler to send a message we had preloaded into a CAN_FRAME variable.

In this way, all traffic is handled by the can handler and it can intelligently parse out CAN frames to hungry object modules waiting for them , and also stream messages onto the bus without collision or panic party.

The GEVCU project is designed such that the core system can be extended with modules that provide support for various pieces of hardware. Designing a new module is not conceptually complex but does require several things to be successful.

Note about formatting: BOLD words are class names. Italic words are file names. Underlined words are methods or members of a class. Methods are postfixed with ().

1. The first order of business is to find an existing module of hopefully the same basic type as your desired new module. For instance, if you hope to add support for an XYZ inverter then maybe you’d like to copy the DmocMotorController class. Rename the files with the same format. Maybe you’d name the files XYZMotorController.cpp and XYZMotorController.h If you cannot find an existing device of the same type then still use an existing set of files. The DmocMotorController class could be used as the basis for most any other device.
2. Rename all of the class references in the copied files as well.
3. Notice that DmocMotorController inherits from MotorController and CanObserver. If you are not creating a motor controller class then inherit from something else. Currently the other good choices are Throttle or Device. Device is always a decent choice if no more specific parent class exists. Inheriting from CanObserver is required if your device needs access to either of the CAN busses.
4. Each device can store data within EEPROM. Each device should create a configuration class that inherits from DeviceConfiguration. The loadConfiguration() and saveConfiguration() methods of DmocMotorController and MotorController can be used as a reference for how to load and save configurations.
5. Each device also must have a unique ID and should set what type of device it is. These are set with getId() and getType(). There is a global list of IDs that you should add your device to. DeviceTypes.h contains both the allowable device types and the ID of each and every device that is compiled into the firmware. You will note that DmocMotorController does not contain getType(). Instead it maintains the parent class version since it is still a motor controller.
6. Next, edit the constructor. Most of the constructor will be custom to your device but you will need to set prefsHandler to use your device ID constant instead of DMOC645. Also, set commonName to a nice, short description of your device.
7. Then there are several edits to make in the setup method. As shown in the DmocMotorController class, one should set up the tick handler, load the EEPROM configuration, call the parent setup (if applicable), and set up canbus handlers (if applicable).
  a. A tick handler allows your device to receive periodic ticks so that it can do processing at set intervals. This might be so that you can send canbus frames or so that you can check for input on one or more pins.
  b. Your class should have a handleTick() method if you have registered a tick handler.
  c. A canbus handler, handleCanFrame(), allows your device to register to receive frames that match the mask. The call to attach has four parameters. The first will basically always be “this”. The second is the ID to match, the third is the mask, and the fourth specifies whether you are interested in standard (false) or extended (true) frames. If you need a quick refresher on masks and IDs: Canbus filtering happens by taking every incoming frame and doing a bitwise AND with each registered mask in turn. The result of this is then compared to the associated ID for that mask. If the two match then your device will receive that frame. For instance, if a frame with 0x23D were to come in and the DmocMotorController had registered a mask of 0x7F0 and an ID of 0x230. 0x23D AND 0x7F0 = 0x230. This does match the ID and so DmocMotorController would get the frame.
  d. Your class should have a handleCanFrame() method if you have registered one or more canbus handlers. This method takes a pointer to a canbus frame as input.
8. As covered above, handleTick() and handleCanFrame() will form the majority of the action in most devices. Many devices will want to be able to send canbus frames out as well. This is done through CanHandler::getInstanceEV() or CanHandler::getInstanceCar(). The MotorController class pre-caches CanHandler::getInstanceEV() into the canHandlerEv member. To send a frame, first create a CAN_FRAME variable, fill it out, and use sendFrame() to send it. The DMOC sendCmd1 method shows how to do this.
9. If your device handler needs access to physical IO then use the systemIO member variable inherent to all devices. This variable references the SystemIO class which has the ability to interact with all of the digital I/O and analog inputs.
10. Now that the device handler has been constructed it is time to connect it with the rest of the system. In GEVCU.ino there is a function called createObjects(). You will need to instantiate your class here. You will also have you add your .h file as an include in GEVCU.h. With this done everything should automatically work. The system uses the PrefsHandler instance you setup in the class constructor to determine whether a given device is enabled and only sets up devices which are enabled.
11. A consequence of above is that you *must* enable your new device before it will do anything. This is done by typing “ENABLE=” followed by the ID of your new device.
1. Create your object.cpp and object.h files for your class. Often it is of help to copy an existing file set and rename them. If your new object is a motorcontroller, for example, use dmocMotorController.cpp and dmocMotorController.h. If it is a charger, copy a charger module.
2. List your device in DeviceTypes.h
3. Add your device as an include in GEVCU.h
4. Revise the createObjects section of GEVCU.ino to instantiate your class there.

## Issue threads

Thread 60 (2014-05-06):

Problems with 1.5.6 Arduino IDE

collin80, 2014-05-06:
The firmware seems to experience random hard freezes if compiled under 1.5.6. As such, don't try to do that right now until the problem is corrected either on our end or Arduino's end.

collin80, 2015-03-15:
Everything seems to work properly in 1.6.0 so don't use 1.5.7 and instead upgrade to 1.6.0 which is the new stable version of the IDE.

Closed 2015-03-15.

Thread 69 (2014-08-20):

Torque slew rate is slow

collin80, 2014-08-20:
This issue could be either in the GEVCU code or in the DMOC or both. When you step on the throttle it doesn't quite respond with the proper haste. There is a lot of throttle smoothing going on on the GEVCU side so that might be the cause or the DMOC might be limiting torque slew rate. This should be investigated and solved one way or the other.

neuweiler, 2017-04-01:
unless you've integrated my code which artificially adds "slew" to the throttle, the response of the throttle class itself is immediate. It might be that analog inputs add some slew. With a CAN bus throttle and Brusa motor controller, the repsonse is immediate. (that's why I added a slew rate in the ArduinoDue branch)

collin80, 2017-04-02:
Yes, subsequent to creating this issue we then got the UQM inverter working. It works perfectly fine. It appears that the issue was solely with the DMOC inverter. It apparently has a torque slew rate setting that needs to be changed. This isn't a GEVCU issue. Closing.

Isaac96, 2019-06-09:
Any recollection on what torque slew rate setting you adjusted in the DMOC? Also, it seems like there's a hard limit on the amps we can draw, or perhaps that's a function of other settings? (Trying to decide if we should replace the controller board on the DMOC with Johannes Huebner's open inverter, but first want to max out the DMOC 645.) Thanks!

collin80, 2019-06-09:
I don't remember. It has been years since I actually used a DMOC in a car. I have a DMOC "on the bench" if by that I mean "it's kind of hooked up in a heap under a shelf." I will try to connect to that DMOC this week and see if I can find the setting.

Isaac96, 2019-06-11:
Thanks Collin. My son (and this is his gihub account I'm writing to you on) has gone through all of your GEVCU code while building our car, and has used your CAN library on several arduinos to control various things like a Leaf BMS and Volt DC-DC. Thanks for the great code!

Isaac96, 2019-06-21:
Collin I wonder if you could send us your par file?

Closed 2017-04-02.

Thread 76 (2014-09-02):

Merge good stuff from ArduinoDue branch into WIP branch

collin80, 2014-09-02:
The official EVTV branch is now based on the WIP branch and not the ArduinoDue branch. However, there were valuable commits to the ArduinoDue branch that should be backported to the WIP branch. So, this will now commence. The inverse should also happen - porting relevant changes to WIP into the ArduinoDue branch. There are some philosophical differences between the two branches but the majority of the code is the same.

collin80, 2015-03-15:
I did end up merging a couple of things back into the main code. That happened some time ago. So, this will be closed now.

Closed 2015-03-15.

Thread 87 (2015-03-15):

Investigate serial buffering between MCU and IChip

collin80, 2015-03-15:
Arduino 1.6.0 includes new code to implement serial TX interrupts. This allows serial writing to be non-blocking most of the time. However, no one knows for sure how this has affected the ichip interface code. Are we filling up the TX buffer? How often does it block if so? Can some of the complications in the ichip param updating code be removed now?

collin80, 2015-03-16:
Is it possible to stop sending updates to the web interface if we know that nobody is listening? Perhaps a 10 minute time out? Can we figure out if anyone is listening?

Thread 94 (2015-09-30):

Outputs trigger on start up

collin80, 2015-09-30:
All outputs trigger for a short time on start up. They soon go to proper state

collin80, 2015-11-18:
This a hardware issue where there isn't a pull down on mosfets so they float active for a moment upon start up. Can be fixed by adding pull downs between the MCU pins and the mosfet driver chips. There is no software fix.

collin80, 2017-04-02:
Was fixed in GEVCU6 by adding the appropriate pull downs. There isn't anything to be done for earlier GEVCU versions so I suppose I should just close this now.

Closed 2017-04-02.

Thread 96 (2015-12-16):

PWM outputs

collin80, 2015-12-16:
GEVCU5 boards are capable of PWM on the outputs but there is currently no support for this functionality in software. It would be nice if it were possible to set up a PWM map on the GUI interface that allows the end user to calibrate the PWM output to how their gauge works.

jrickard, 2015-12-16:
The PWM output has a problem I think.  Maybe I'm wrong.  Get me
straightened out.  With this low side switching isn't ON off and OFF is on
and so forth?  So no output is a solid 12v and as we increase the pulse
width the PWM output would go DOWN instead of up.  This is a little
counterintuitive.

Jack Rickard

On Tue, Dec 15, 2015 at 8:44 PM, Collin Kidder <notifications@github.com>
wrote:

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

--
http://www.EVTV.me <http://EVTV.me>

Electric Vehicle Television - KickinGas  - One Car at a Time.

jrickard, 2015-12-16:
You should have a truckload full of shit by now I guess?

I spent the entire day with your father.  We rather hit it off.  He may be
me.  Or I may be him.  We had much in common in almost all directions.  He
doesn't smoke of course and is quite trim, but beyond that....

I sent a Leaf motor and inverter.  He was rather agonizing over the risk of
whether you could do it or not.  I assured him that you could easily now
that you have a Leaf to capture from, but I would supply it in any event.
I'm sure it will be more work setting up the test bench than it is reverse
engineering the CAN commands.  Could be wrong.  But there's a lot of Leaf
stuff floating around out there already and I'm not seeing much trickery.

I would like to be able to just buy these from the Nissan dealers, add a
GEVCU, and sell them.  I guess they are supposedly rated at 90kw rather
than the 100kw of the UQM, but other than that, appears to be very similar.

I kind of put the squeeze on to talk your father into doing a plastic or
fiberglass reproduction of a 190SL in electric with a Tesla drive unit in
it.  I think you'd do extremely well with that. I'd probably have to have
one...

Jack Rickard

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

--
http://www.EVTV.me <http://EVTV.me>

Electric Vehicle Television - KickinGas  - One Car at a Time.

collin80, 2015-12-16:
Yes, you are correct. The outputs are low side and switch ground so PWM is completely backward of what you would normally expect. High duty cycle corresponds to a lower average voltage and lower duty cycle raises the average voltage. So, for voltage sensitive gauges the whole thing is backward. For gauges that count pulses it can work as normal as you would still get the correct number of pulses, just with reverse polarity. I think that would still work OK.

A somewhat bigger issue is how irritating it is if you need a frequency controlled gauge. Controlling the frequency of the PWM outputs isn't a lot of fun. It's much simpler when you can just control the duty cycle.

neuweiler, 2017-04-01:
In ArduinoDue branch SystemIO::handleTick() (around line 100) I use PWM to output the estimated SOC to a DOUT. It is reversed due to the MOSFET. Works pretty fine for my digital fuel gauge with a resistor and capacitor to smoothen out the PWM to an analog signal.

collin80, 2017-04-02:
Thanks for the heads up. Yes, I can see how you've implemented it. Using analogWrite works fine but as you know it's inverted and also does not support setting the frequency. Normally you don't need to change frequency but I had an application where I had to. I've still got that code in a private branch, perhaps I'll see what it would take to bring it into mainline.

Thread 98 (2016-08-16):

Gevcu looses halve of the programmed data

Elegancec, 2016-08-16:
Hi, the GEVCU has lost halve of the data (throttle settings like min max of T1 are still stored, but lost are: All digital inputs and outputs, battery voltage, torque, precharge delay.
This happened now the third time and I need to reprogram the controller with the data, to go ahead whith driving.

Is this behaviour known? How can I solve it? Im driving the car since december and in happened in total three times, just occasionally.

Additionally, I can only reprogram it with some computers, but not with my android 5 phone. It doesn't find the gevcu.

cgalpin, 2016-08-17:
When the settings are read and the checksum is invalid it resets the values. One way to verify this is what’s happening and to help alleviate the issue is to change the defaults in config.h to sane values for your vehicle, with some difference that you can identify from your normal settings but still get you home.  Then when it happens again if you get these values then you know what it is.

If it is this, then I am not sure why it’s happening, but we could try change the code to re-read the settings a couple of times if the checksum is invalid before resetting the values. Maybe it’s a glitch and it will succeed on the 2nd or 3rd attempt.

hth
charles

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

neuweiler, 2017-04-01:
I experience this too from time to time and it's very annoying (usually makes me arrive late at work). I suspect that it happens when the power is cut while GEVCU is still writing a page to the EEPROM (e.g. when storing the energy consumption or changing the config and not waiting long enough to restart).

Elegancec, 2017-04-01:
Hi Michael,

I have written the parameters into the config.h file, so if it looses
the data, it will automatically restart with the preset data again. Up
to now I don't have any problems.

BR

Hanno

Am 01.04.2017 um 17:00 schrieb Michael Neuweiler:
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

collin80, 2017-04-02:
Yes, I'm still not entirely sure of *why* it happens. It happens sometimes seemingly randomly. It happens more to some people than others. It does seem like it must be some sort of power glitch or write while powering off. The EEPROM chip takes a long time to write (something like 7 miliiseconds) and the power taper can take longer than that. When that happens it is possible that the EEPROM would try to write while the voltage is insufficient to do so. The EEPROM is supposed to detect this as well I think but might have trouble if the write starts and then the power drops out mid way through. I've done testing to turn off the processor very rapidly if the power is dropping out. I can make it do that but I'm not entirely convinced it solves the problem. If either of you want to try you could add the below line into the setup() function in GEVCU.ino and see if it does anything:

SUPC->SUPC_SMMR = 0xA | (1<<8) | (1<<12);

The line causes the CPU to go into reset at 2.8V on the 3.3V input line. This causes it to go into reset very quickly after the power starts to die. I've looked at the power rail on drop out and with this line the voltage tapers off much more slowly after the CPU goes into reset. The CPU is the main consumer of power on the 3.3V rail ordinarily. With the line in effect it *should* be possible for a write issued by the CPU to go through as the power stays steady for long enough to write. But, it's kind of hard to test that thoroughly enough.

I suppose the line probably doesn't hurt anything so after some more testing I will likely add it into GEVCU for all subsequent releases.

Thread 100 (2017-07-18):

Installing on Arduino Due to Control late model car?

jjwallace, 2017-07-18:
Hello, me again.
We are converting a late model car which has a stock ECU and would like to replace it with the GEVCU.
Can it control ABS, stability and airbag?
Can it export data to the cluster and speedometer so that it works?
Are these pins correct for Arduino?  Pins 9/10 are canbus high and low?

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

collin80, 2017-07-19:
Yes, 9 is high, 10 is low for the first CAN bus. All of the grounds are connected and equivalent. You can export data to your custer and speedo so long as they are CAN based. This is very likely on a late model car. Also, you could control ABS so long as those signals were all routed over CAN. I can't say for sure whether this is true or not. I know that late model cars route an awful lot over CAN so it is possible. But, I can't vouch for every vehicle. For both ABS and the cluster/speedo your best bet is to first get many captures from a live, running car to see if the data you're looking for is where you think it is. Here is a link to a bunch of community edited DBC files that may have data that you could use: https://github.com/commaai/opendbc

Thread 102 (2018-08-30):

Use this on an electric car

amrithmmh, 2018-08-30:
I am working on a college project that needs a whole CAN bus system to control a car. The messages will be generated by a computer and send to the controller and then actuators . Can this project be used for my project?   note: currently the car have no ECU or CAN bus system

collin80, 2018-08-30:
Yeah, that's basically *all* it's for. ;) The whole point is to use it as the main ECU for an electric car in order to control all of the various other modules.

amrithmmh, 2018-08-31:
@collin80 I am new to this topic.
I have a question.Is there any Electronic control units that can be used to control accelerator  brake and steering ?
currently the car has only an electric accelerator pedal , brake is mechanical and steering is also mechanical

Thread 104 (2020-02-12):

Compiling Code Throws Warnings

chadman98126, 2020-02-12:
Colin/Jack:

When compiling the GEVCU code, the latest version of the Arduino IDE (1.8.11) throws the following errors when writing text strings, logging, etc.  - several dozen actually.

obviously these are warnings and the code will still compile, but pretty cumbersome having to debug around these.  appears to be a syntax issue between C/C++. one approach might be to use
const char* vs. char* in each of the declarations -- the issue is primarily setting commonName and when sending log messages -- there may be others, but that's as far as I've gotten through all the warnings.

your thoughts on whether this is a really BAD idea or other options - as you've been closest to the code throughout.

note: I'm loathe to suppress the warnings in the IDE, etc. for obvious reasons, but if that's the only practical option...

--------

sketch/CanBrake.cpp: In constructor 'CanBrake::CanBrake()':
sketch/CanBrake.cpp:40:13: warning: deprecated conversion from string constant to 'char*' [-Wwrite-strings]
  commonName = "CANBus brake";
             ^
sketch/CanBrake.cpp: In member function 'virtual void CanBrake::setup()':
sketch/CanBrake.cpp:46:71: warning: deprecated conversion from string constant to 'char*' [-Wwrite-strings]
  Logger::info("add device: CanBrake (id: %X, %X)", CANBRAKEPEDAL, this);

chadman98126, 2020-02-12:
note: I updated char* to const char* in device.h and device.cpp and the bulk of these warnings go away.   spelunking through the remaining 4 or 5 in GEVCU.ino

but again, not sure if these were oversights -- as the code elsewhere uses const char* -- of if these were intentional.

chadman98126, 2020-02-12:
these are the remaining errors.  not as clear to me how to resolve, but will continue to dig.

---------
/Users/chad/Documents/Arduino/GEVCU/GEVCU.ino: In function 'void initializeDevices()':
/Users/chad/Documents/Arduino/GEVCU/GEVCU.ino:230:66: warning: deprecated conversion from string constant to 'char*' [-Wwrite-strings]
  Logger::info("add: Heartbeat (id: %X, %X)", HEARTBEAT, heartbeat);
                                                                  ^
/Users/chad/Documents/Arduino/GEVCU/GEVCU.ino: In function 'void setup()':
/Users/chad/Documents/Arduino/GEVCU/GEVCU.ino:261:28: warning: deprecated conversion from string constant to 'char*' [-Wwrite-strings]
  Logger::info("TWI init ok");
                            ^
/Users/chad/Documents/Arduino/GEVCU/GEVCU.ino:263:62: warning: deprecated conversion from string constant to 'char*' [-Wwrite-strings]
  Logger::info("add MemCache (id: %X, %X)", MEMCACHE, memCache);
                                                              ^
/Users/chad/Documents/Arduino/GEVCU/GEVCU.ino:268:42: warning: deprecated conversion from string constant to 'char*' [-Wwrite-strings]
        Logger::info("Initializing EEPROM");
                                          ^
/Users/chad/Documents/Arduino/GEVCU/GEVCU.ino:272:60: warning: deprecated conversion from string constant to 'char*' [-Wwrite-strings]
           else {Logger::info("Using existing EEPROM values");}//checksum is good, read in the values stored in EEPROM
                                                            ^
/Users/chad/Documents/Arduino/GEVCU/GEVCU.ino:285:30: warning: deprecated conversion from string constant to 'char*' [-Wwrite-strings]
  Logger::info("SYSIO init ok");
                              ^
/Users/chad/Documents/Arduino/GEVCU/GEVCU.ino:293:29: warning: deprecated conversion from string constant to 'char*' [-Wwrite-strings]
  Logger::info("System Ready");

chadman98126, 2020-02-12:
again, looks to be an issue with char* declarations in logger.h and logger.cpp

now, getting very wary of making these changes...  (as Logger is used *everywhere*)

chadman98126, 2020-02-12:
and maybe only specific to Logger::info??

collin80, 2020-02-12:
It should be fine to do what you're doing. The code for GEVCU is partly kind of old and the good compiler warnings didn't trigger back then. So, we just kind of never did it right and the compiler didn't complain. Now it properly complains. It's best to make all the string constants "const" anyway as that ensures that they'll be left in FLASH instead of loaded into RAM where they needn't be.

chadman98126, 2020-02-12:
Problem is the declarations in logger.h and .cpp are tripping me up — I’m not a super coder.  they are char *variableName (vs char* variableName) and not close enough to the original code to get it to compile. After making changes to logger - all sort of things go hairy.

cgalpin, 2020-02-13:
What’s hairy?

In both logger.h and logger.cpp you should be able to change all "char *message” to “const char *message” in the method arguments without issues.

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

chadman98126, 2020-02-13:
I tried that and I got a raft of errors. I wasn’t sure if “const char *message” was a valid declaration.

cgalpin, 2020-02-13:
I downloaded Arduino IDE 1.8.11, and the latest GEVCU, installed the Due board and selected it and compiled. I then changed all the instances that gave warning and it compiled cleanly.

If you change the function declaration in a .h, you need to also do the same in the .cpp file

Here is there diff.

hth
charles

$ diff -r GEVCU GEVCU-master
diff -r GEVCU/Device.cpp GEVCU-master/Device.cpp
43c43
< const char* Device::getCommonName() {
---
> char* Device::getCommonName() {
diff -r GEVCU/Device.h GEVCU-master/Device.h
60c60
< 	const char* getCommonName();
---
> 	char* getCommonName();
69c69
< 	const char *commonName;
---
> 	char *commonName;
diff -r GEVCU/GEVCU.ino GEVCU-master/GEVCU.ino
92,104c92,104
< sendWiReach((char *)"AT+iHIF=1");//Host connection set to serial port
< sendWiReach((char *)"AT+iBDRF=9");//Automatic baud rate on host serial port
< sendWiReach((char *)"AT+iRPG=secret"); //Password for iChip wbsite
< sendWiReach((char *)"AT+iWPWD=secret");//Password for our website
< sendWiReach((char *)"AT+iWST0=0");//Connection security wap/wep/wap2 to no security
< sendWiReach((char *)"AT+iWLCH=4");  //Wireless channel
< sendWiReach((char *)"AT+iWLSI=GEVCU");//SSID
< sendWiReach((char *)"AT+iWSEC=1");//IF security is used, set for WPA2-AES
< sendWiReach((char *)"AT+iSTAP=1");//Act as AP
< sendWiReach((char *)"AT+iDIP=192.168.3.10");//default ip - must be 10.x.x.x
< sendWiReach((char *)"AT+iDPSZ=8");//DHCP pool size
< sendWiReach((char *)"AT+iAWS=1");//Website on
< sendWiReach((char *)"AT+iDOWN");//Powercycle reset
---
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
diff -r GEVCU/Logger.cpp GEVCU-master/Logger.cpp
37c37
< void Logger::debug(const char *message, ...) {
---
> void Logger::debug(char *message, ...) {
50c50
< void Logger::debug(DeviceId deviceId, const char *message, ...) {
---
> void Logger::debug(DeviceId deviceId, char *message, ...) {
63c63
< void Logger::info(const char *message, ...) {
---
> void Logger::info(char *message, ...) {
76c76
< void Logger::info(DeviceId deviceId, const char *message, ...) {
---
> void Logger::info(DeviceId deviceId, char *message, ...) {
89c89
< void Logger::warn(const char *message, ...) {
---
> void Logger::warn(char *message, ...) {
102c102
< void Logger::warn(DeviceId deviceId, const char *message, ...) {
---
> void Logger::warn(DeviceId deviceId, char *message, ...) {
115c115
< void Logger::error(const char *message, ...) {
---
> void Logger::error(char *message, ...) {
128c128
< void Logger::error(DeviceId deviceId, const char *message, ...) {
---
> void Logger::error(DeviceId deviceId, char *message, ...) {
141c141
< void Logger::console(const char *message, ...) {
---
> void Logger::console(char *message, ...) {
201c201
< void Logger::log(DeviceId deviceId, LogLevel level, const char *format, va_list args) {
---
> void Logger::log(DeviceId deviceId, LogLevel level, char *format, va_list args) {
246c246
< void Logger::logMessage(const char *format, va_list args) {
---
> void Logger::logMessage(char *format, va_list args) {
372a373,374
>
>
diff -r GEVCU/Logger.h GEVCU-master/Logger.h
40,48c40,48
< 	static void debug(const char *, ...);
< 	static void debug(DeviceId, const char *, ...);
< 	static void info(const char *, ...);
< 	static void info(DeviceId, const char *, ...);
< 	static void warn(const char *, ...);
< 	static void warn(DeviceId, const char *, ...);
< 	static void error(const char *, ...);
< 	static void error(DeviceId, const char *, ...);
< 	static void console(const char *, ...);
---
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
57,58c57,58
< 	static void log(DeviceId, LogLevel, const char *format, va_list);
< 	static void logMessage(const char *format, va_list args);
---
> 	static void log(DeviceId, LogLevel, char *format, va_list);
> 	static void logMessage(char *format, va_list args);
62a63,64
>
>

chadman98126, 2020-02-13:
I will try this. Much thanks!

chadman98126, 2020-02-13:
got a subsequent similar error on ThottleDetector.cpp, but resolved in s similar way.
all the char* errors now seem to be resolved.

now getting the following:

sketch/MemCache.cpp: In member function 'boolean MemCache::Write(uint32_t, void*, uint16_t)':
sketch/MemCache.cpp:214:81: warning: pointer of type 'void *' used in arithmetic [-Wpointer-arith]
       pages[c].data[(uint16_t)((address+count) & 0x00FF)] = *(uint8_t *)(data + count);
                                                                                 ^
sketch/MemCache.cpp: In member function 'boolean MemCache::Read(uint32_t, void*, uint16_t)':
sketch/MemCache.cpp:274:27: warning: pointer of type 'void *' used in arithmetic [-Wpointer-arith]
       *(uint8_t *)(data + count) = pages[c].data[(uint16_t)((address+count) & 0x00FF)];

will take a run at these next

chadman98126, 2020-02-13:
disregard the last, it appears the Arduino IDE was parsing MemCache.cpp incorrectly and missing some of the declaration.  compiling a second time, the warnings go away.

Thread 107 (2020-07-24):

Support newer version of Arduino IDE

timlaw55, 2020-07-24:
The readme specifies the need to use Arduino IDE 1.5.4.  It will not run on OS X Catalina.  Are there specific reasons requiring this version?

collin80, 2020-07-24:
Probably not but maybe. The thing is, the source code for GEVCU is right around 5-7 years old at this point. Back then the most recent IDE version probably was 1.5.4. So, the idea, as far as I recall, was to require a fairly new IDE version so that people wouldn't try to use a super old version. The newer 1.8.X release which is current should work. There have been some architectural changes to the Arduino system over the years but the Arduino Due core that is used by GEVCU hasn't had updates in quite some time so it is likely pretty stable and just about the same as it was 5 years ago. The GEVCU6 branch that supports the newer V6 hardware was branched from this code and it has been recently compiled on 1.8.X versions and works fine. So, I have reason to believe it would work fine but I can't promise that.

cgalpin, 2020-07-24:
I can confirm it works fine on 1.8.11 on OSX - just tried it the other day

timlaw55, 2020-07-24:
I was using 1.8.x.  I added my new motor controller and got everything compiling.  When I tried to push it to GEVCU 5.2 I got this error :

    No device found on cu.usbmodem14101
    An error occurred while uploading the sketch

I know the port is good because I can interact with the GEVCU through the integrated terminal.  I tried bringing up 1.5.4 IDE version in a VM but I can't even get that to build.  Idealy I would rather use the newer version.  Thanks @cgalpin for verifying it works.  Now if I could figure out why it fails to push the code.  Do I need to crack open the case and press a button or something to get it to accept programming?  Any other suggestions for why I would get that error?

timlaw55, 2020-07-24:
After failing a number of times, I turned on verbose logging and it uploaded. :/  I show a new option for UQM.  Now on to the UQM CAN spec documents to figure out what I need to send to get the motor spinning...

Closed 2020-07-24.

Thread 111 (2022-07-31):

Removing link http://www.gevcu.org/ since it’s spam

robomaniac, 2022-07-31:
Have you thought of removing the link to your website since it’s now spam and pop up. (Varies if you use safari, chrome, phone or computer) Or you could redirect it to somewhere else.
http://www.gevcu.org/

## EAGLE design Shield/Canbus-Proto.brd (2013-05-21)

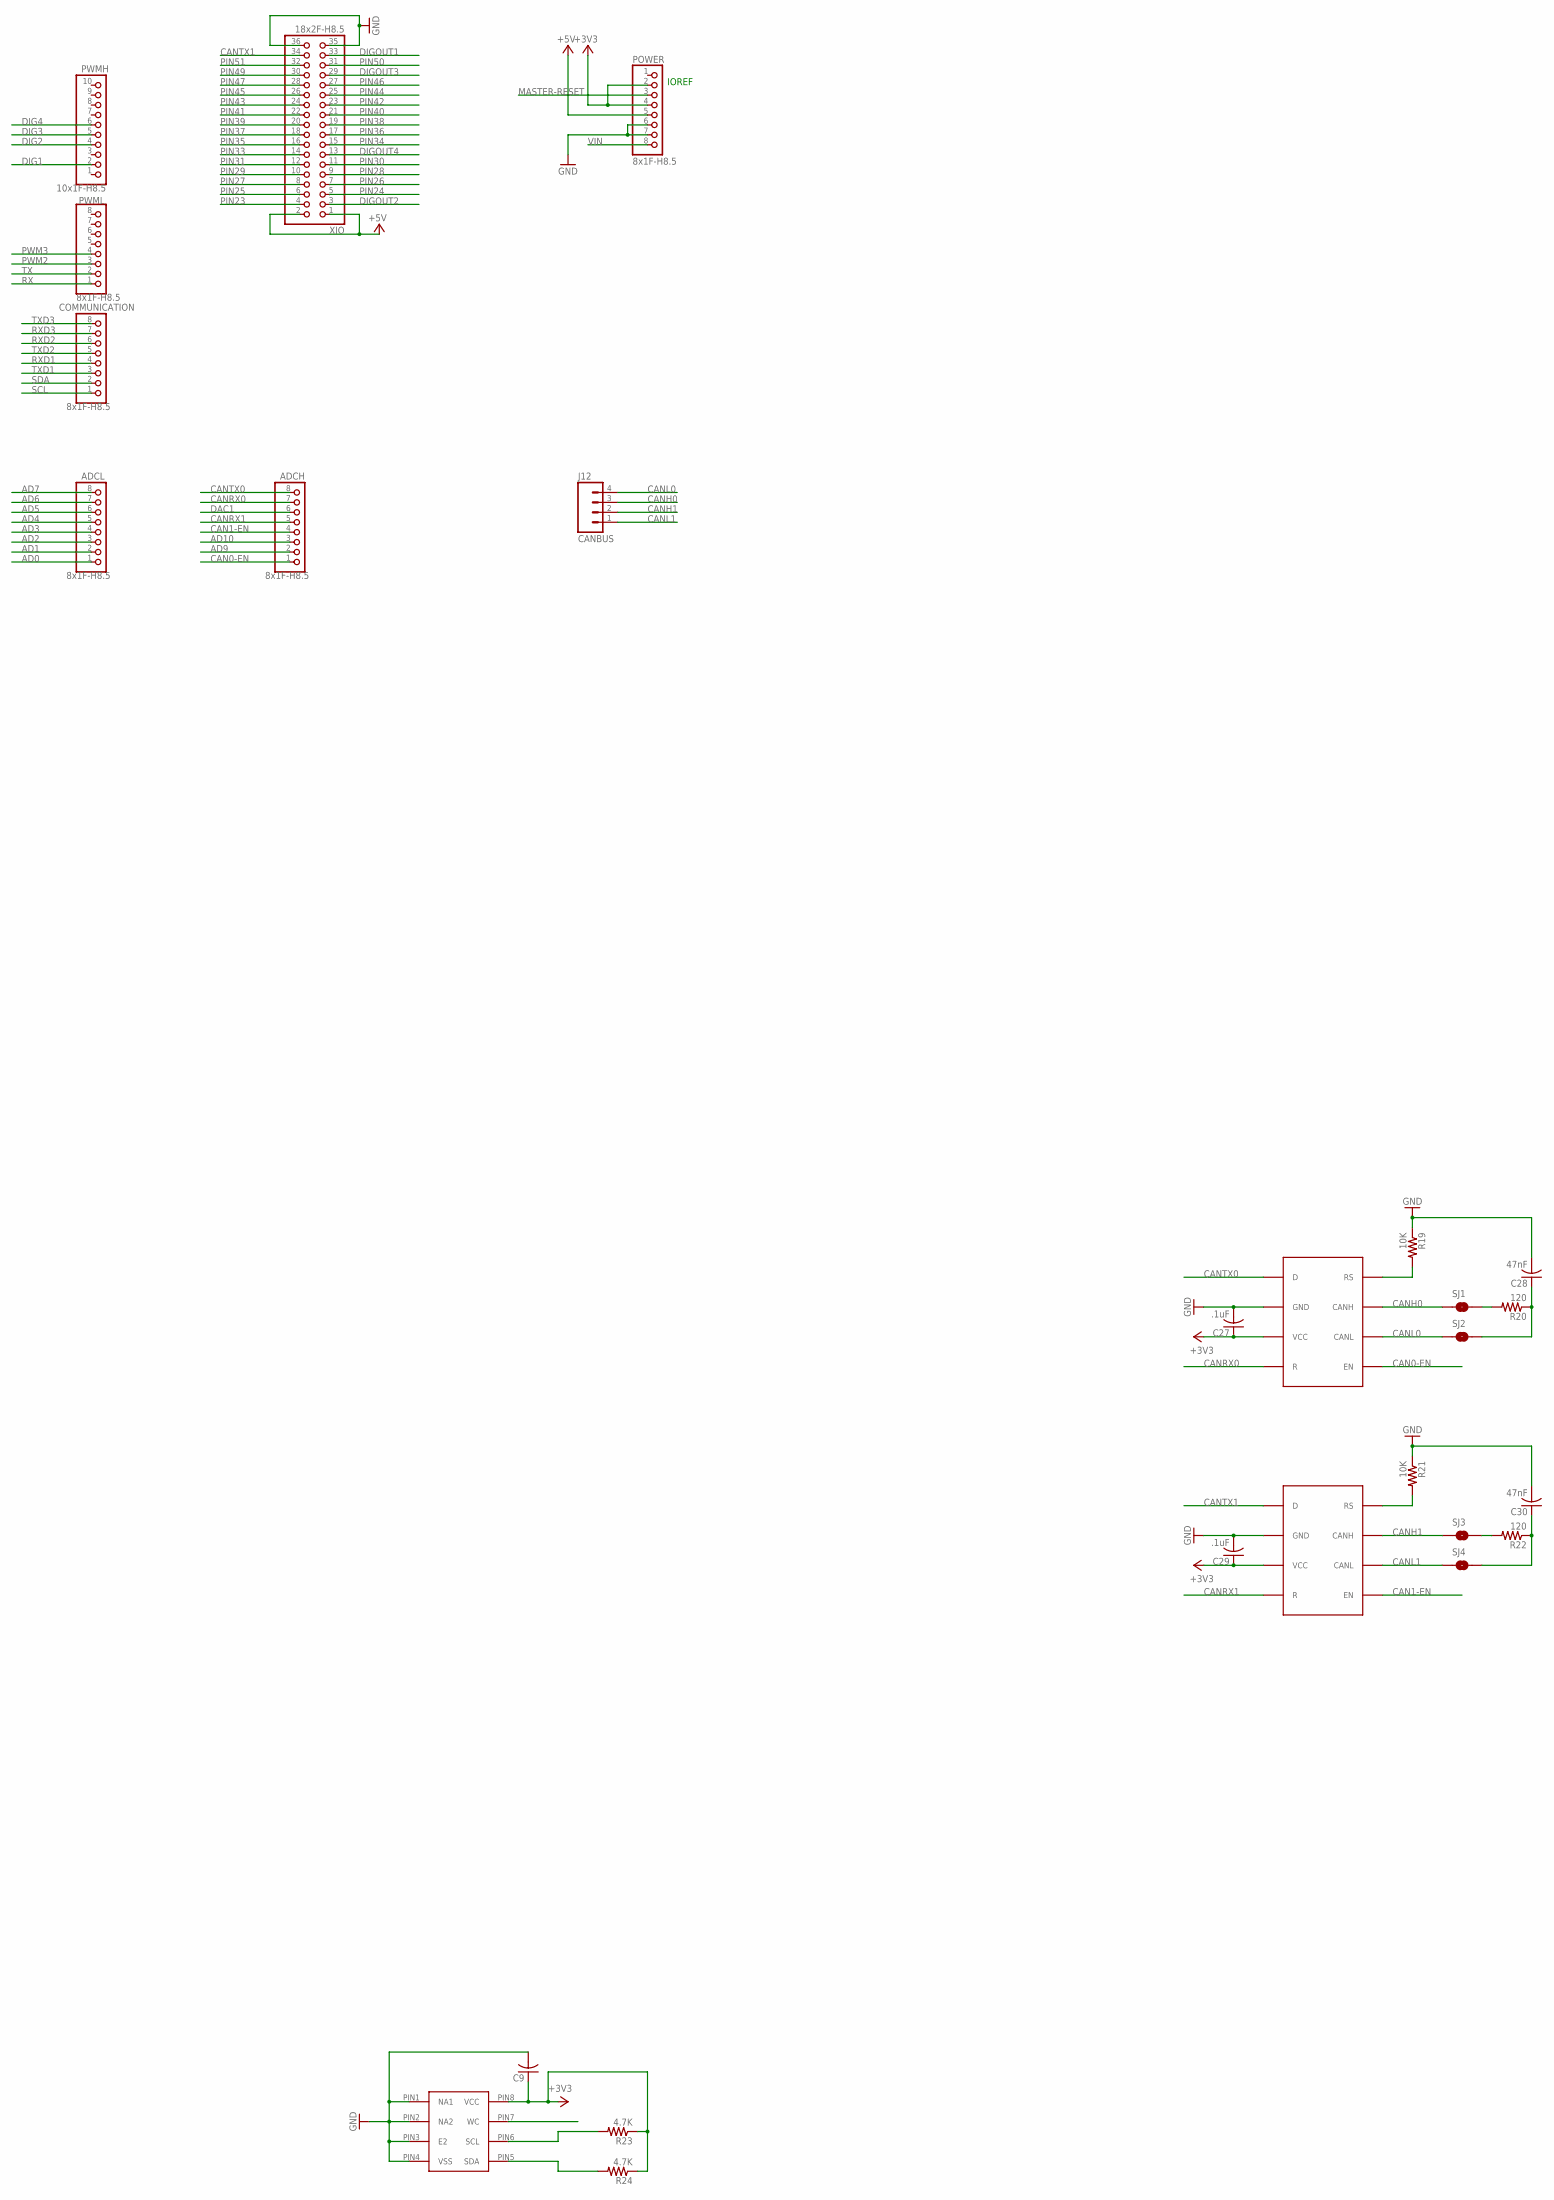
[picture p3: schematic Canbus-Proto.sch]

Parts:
ADCH: 8x1F-H8.5; 1X08
ADCL: 8x1F-H8.5; 1X08
C9: C-USC0603; C0603
C27, C29: .1uF; C0603
C28, C30: 47nF; C0603
COMMUNICATION: 8x1F-H8.5; 1X08
J12: CANBUS; 1X04
POWER: 8x1F-H8.5; 1X08
PWMH: 10x1F-H8.5; 1X10
PWML: 8x1F-H8.5; 1X08
R19, R21: 10K; R0603
R20, R22: 120; R0603
R23, R24: 4.7K; R0603
SJ1, SJ2, SJ3, SJ4: SOLDERJUMPERNO; SJ_2S-NO
U$2, U$6: SN65HVD234; SOIC8
U$5: M24M02-DRMN6TP; SOIC8
XIO: 18x2F-H8.5; 2X18

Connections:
+3V3: C9.1, C27.1, C29.1, POWER.2, POWER.4, R23.1, R24.1, U$2.PIN3 (VCC), U$5.PIN8 (VCC), U$6.PIN3 (VCC)
+5V: POWER.5, XIO.1, XIO.2
AD0: ADCL.1
AD1: ADCL.2
AD2: ADCL.3
AD3: ADCL.4
AD4: ADCL.5
AD5: ADCL.6
AD6: ADCL.7
AD7: ADCL.8
AD9: ADCH.2
AD10: ADCH.3
CAN0-EN: ADCH.1, U$6.PIN5 (EN)
CAN1-EN: ADCH.4, U$2.PIN5 (EN)
CANH0: J12.3, SJ1.1, U$6.PIN7 (CANH)
CANH1: J12.2, SJ3.1, U$2.PIN7 (CANH)
CANL0: J12.4, SJ2.1, U$6.PIN6 (CANL)
CANL1: J12.1, SJ4.1, U$2.PIN6 (CANL)
CANRX0: ADCH.7, U$6.PIN4 (R)
CANRX1: ADCH.5, U$2.PIN4 (R)
CANTX0: ADCH.8, U$6.PIN1 (D)
CANTX1: U$2.PIN1 (D), XIO.34
DAC1: ADCH.6
DIG1: PWMH.2
DIG2: PWMH.4
DIG3: PWMH.5
DIG4: PWMH.6
DIGOUT1: XIO.33
DIGOUT2: XIO.3
DIGOUT3: XIO.29
DIGOUT4: XIO.13
GND: C9.2, C27.2, C28.2, C29.2, C30.2, POWER.6, POWER.7, R19.1, R21.1, U$2.PIN2 (GND), U$5.PIN1 (NA1), U$5.PIN2 (NA2), U$5.PIN3 (E2), U$5.PIN4 (VSS), U$6.PIN2 (GND), XIO.35, XIO.36
MASTER-RESET: POWER.3
unnamed: R19.2, U$6.PIN8 (RS)
unnamed: C28.1, R20.1, SJ2.2
unnamed: R20.2, SJ1.2
unnamed: R21.2, U$2.PIN8 (RS)
unnamed: C30.1, R22.1, SJ4.2
unnamed: R22.2, SJ3.2
PIN23: XIO.4
PIN24: XIO.5
PIN25: XIO.6
PIN26: XIO.7
PIN27: XIO.8
PIN28: XIO.9
PIN29: XIO.10
PIN30: XIO.11
PIN31: XIO.12
PIN33: XIO.14
PIN34: XIO.15
PIN35: XIO.16
PIN36: XIO.17
PIN37: XIO.18
PIN38: XIO.19
PIN39: XIO.20
PIN40: XIO.21
PIN41: XIO.22
PIN42: XIO.23
PIN43: XIO.24
PIN44: XIO.25
PIN45: XIO.26
PIN46: XIO.27
PIN47: XIO.28
PIN49: XIO.30
PIN50: XIO.31
PIN51: XIO.32
PWM2: PWML.3
PWM3: PWML.4
RX: PWML.1
RXD1: COMMUNICATION.4, U$5.PIN7 (WC)
RXD2: COMMUNICATION.6
RXD3: COMMUNICATION.7
SCL: COMMUNICATION.1, R23.2, U$5.PIN6 (SCL)
SDA: COMMUNICATION.2, R24.2, U$5.PIN5 (SDA)
TX: PWML.2
TXD1: COMMUNICATION.3
TXD2: COMMUNICATION.5
TXD3: COMMUNICATION.8
VIN: POWER.8

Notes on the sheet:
IOREF

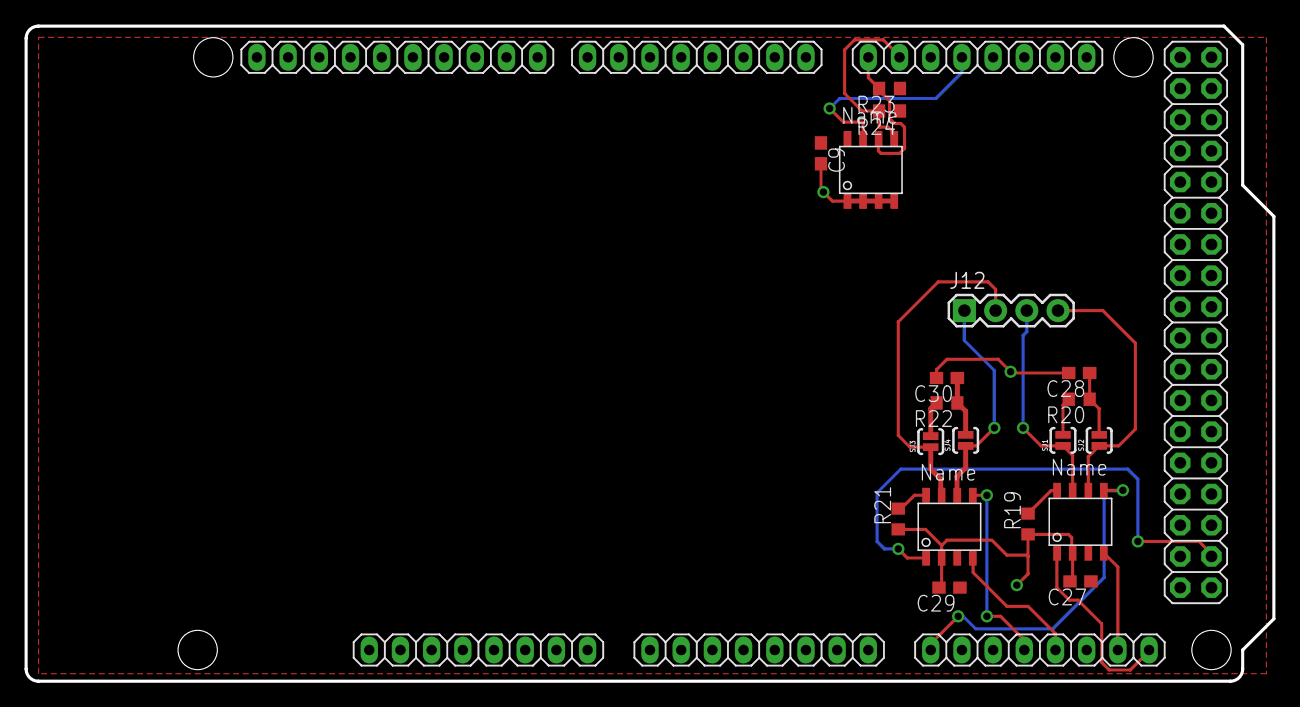
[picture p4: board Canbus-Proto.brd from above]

Board: 2 copper layers, 101.6 x 53.3 mm, 26 parts (0 on the bottom side), 22 nets.

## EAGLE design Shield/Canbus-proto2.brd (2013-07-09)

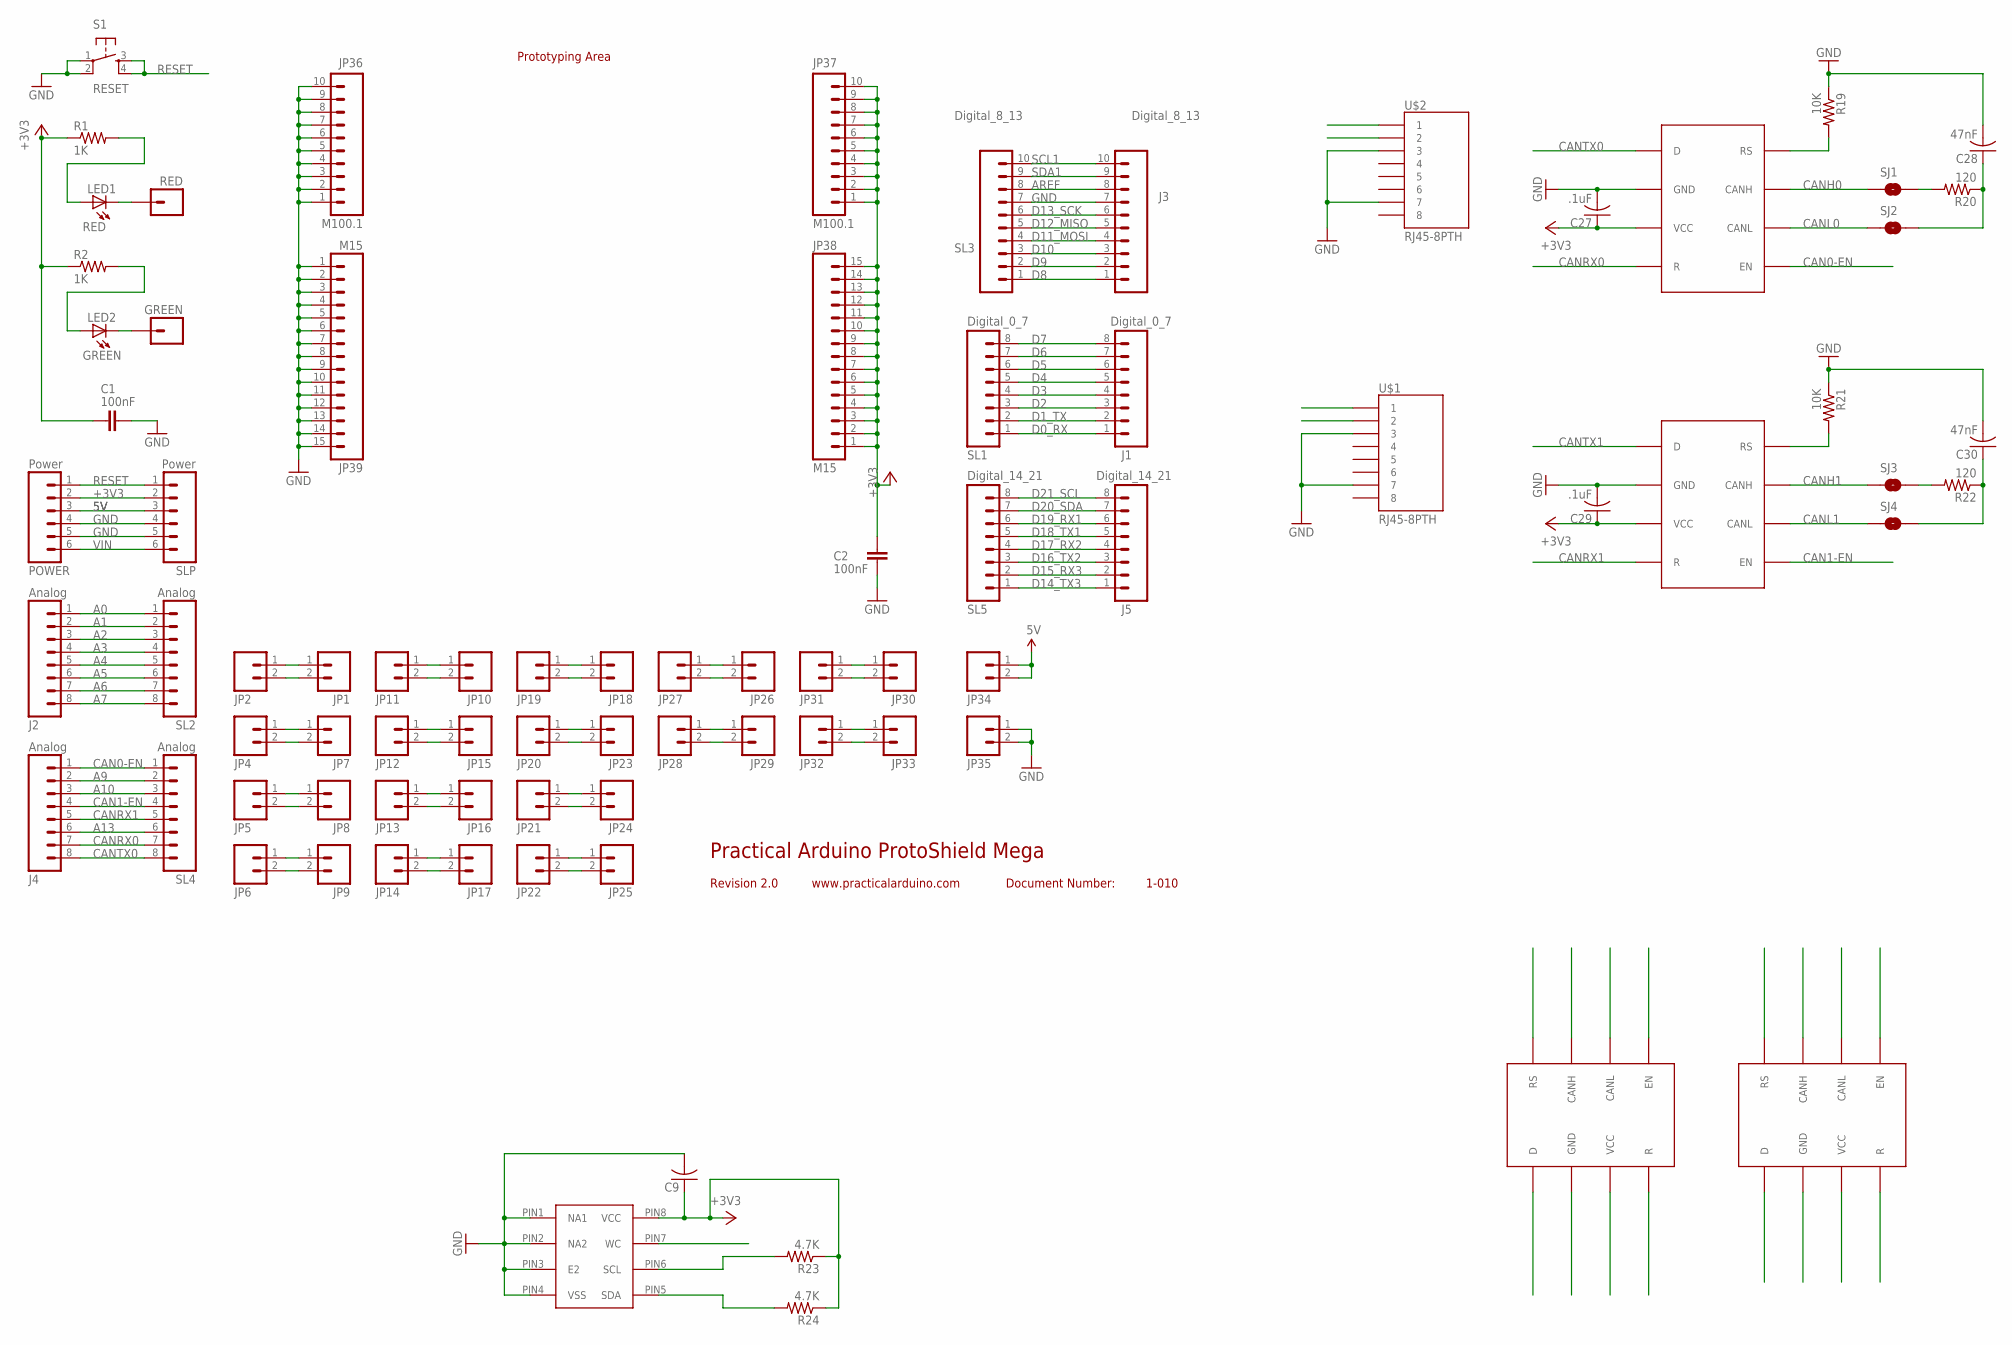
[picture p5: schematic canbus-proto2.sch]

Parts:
C1, C2: 100nF; 0603-CAP
C9: C-USC0603; C0603
C27, C29: .1uF; C0603
C28, C30: 47nF; C0603
GREEN: M01PTH; 1X01
J1: Digital_0_7; 1X08
J2, J4: Analog; 1X08
J3: Digital_8_13; 1X10
J5: Digital_14_21; 1X08
JP1, JP2, JP4, JP5, JP6, JP7, JP8, JP9, JP10, JP11, JP12, JP13, JP14, JP15, JP16, JP17, JP18, JP19, JP20, JP21, JP22, JP23, JP24, JP25, JP26, JP27, JP28, JP29, JP30, JP31, JP32, JP33, JP34, JP35: M02PTH; 1X02
JP36, JP37: M100.1; 1X10@1
JP38, JP39: M15; 1X15
LED1: RED; LED-0603
LED2: GREEN; LED-0603
POWER: Power; 1X06
R1, R2: 1K; R0603
R19, R21: 10K; R0603
R20, R22: 120; R0603
R23, R24: 4.7K; R0603
RED: M01PTH; 1X01
S1: RESET; TACTILE-PTH
SJ1, SJ2, SJ3, SJ4: SOLDERJUMPERNO; SJ_2S-NO
SL1: Digital_0_7; 1X08
SL2, SL4: Analog; 1X08
SL3: Digital_8_13; 1X10
SL5: Digital_14_21; 1X08
SLP: Power; 1X06
U$1, U$2: RJ45-8PTH; RJ45-8
U$3, U$4, U$7, U$8: SN65HVD234; SOIC8
U$6: M24M02-DRMN6TP; SOIC8

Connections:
5V: JP34.1, JP34.2, POWER.3, SLP.3
+3V3: C1.1, C2.1, C9.1, C27.1, C29.1, JP37.1, JP37.2, JP37.3, JP37.4, JP37.5, JP37.6, JP37.7, JP37.8, JP37.9, JP37.10, JP38.1, JP38.2, JP38.3, JP38.4, JP38.5, JP38.6, JP38.7, JP38.8, JP38.9, JP38.10, JP38.11, JP38.12, JP38.13, JP38.14, JP38.15, POWER.2, R1.1, R2.1, R23.1, R24.1, SLP.2, U$6.PIN8 (VCC), U$7.PIN3 (VCC), U$8.PIN3 (VCC)
A0: J2.1, SL2.1
A1: J2.2, SL2.2
A2: J2.3, SL2.3
A3: J2.4, SL2.4
A4: J2.5, SL2.5
A5: J2.6, SL2.6
A6: J2.7, SL2.7
A7: J2.8, SL2.8
A9: J4.2, SL4.2
A10: J4.3, SL4.3
A13: J4.6, SL4.6
AREF: J3.8, SL3.8
B1: U$3.PIN8 (RS)
B2: U$3.PIN7 (CANH)
B3: U$3.PIN6 (CANL)
B4: U$3.PIN5 (EN)
B5: U$3.PIN1 (D)
B6: U$3.PIN2 (GND)
B7: U$3.PIN3 (VCC)
B8: U$3.PIN4 (R)
B9: U$4.PIN8 (RS)
B10: U$4.PIN7 (CANH)
B11: U$4.PIN6 (CANL)
B12: U$4.PIN5 (EN)
B13: U$4.PIN4 (R)
B14: U$4.PIN3 (VCC)
B15: U$4.PIN2 (GND)
B16: U$4.PIN1 (D)
CAN0-EN: J4.1, SL4.1, U$7.PIN5 (EN)
CAN1-EN: J4.4, SL4.4, U$8.PIN5 (EN)
CANH0: SJ1.1, U$2.1, U$7.PIN7 (CANH)
CANH1: SJ3.1, U$1.1, U$8.PIN7 (CANH)
CANL0: SJ2.1, U$2.2, U$7.PIN6 (CANL)
CANL1: SJ4.1, U$1.2, U$8.PIN6 (CANL)
CANRX0: J4.7, SL4.7, U$7.PIN4 (R)
CANRX1: J4.5, SL4.5, U$8.PIN4 (R)
CANTX0: J4.8, SL4.8, U$7.PIN1 (D)
CANTX1: JP32.2, JP33.2, U$8.PIN1 (D)
D0_RX: J1.1, SL1.1
D1: JP10.2, JP11.2
D1_TX: J1.2, SL1.2
D2: J1.3, SL1.3
D3: J1.4, SL1.4
D4: J1.5, SL1.5
D5: J1.6, SL1.6
D6: J1.7, SL1.7
D7: J1.8, SL1.8
D8: J3.1, SL3.1
D9: J3.2, SL3.2
D10: J3.3, SL3.3
D11: JP10.1, JP11.1
D11_MOSI: J3.4, SL3.4
D12: JP18.2, JP19.2
D12_MISO: J3.5, SL3.5
D13: JP18.1, JP19.1
D13_SCK: J3.6, SL3.6
D14: JP26.2, JP27.2
D14_TX3: J5.1, SL5.1
D15: JP26.1, JP27.1
D15_RX3: J5.2, SL5.2
D16: JP30.2, JP31.2
D16_TX2: J5.3, SL5.3
D17: JP30.1, JP31.1
D17_RX2: J5.4, SL5.4
D18_TX1: J5.5, SL5.5, U$6.PIN7 (WC)
D19_RX1: J5.6, SL5.6
D20_SDA: J5.7, R24.2, SL5.7, U$6.PIN5 (SDA)
D21_SCL: J5.8, R23.2, SL5.8, U$6.PIN6 (SCL)
D22: JP1.2, JP2.2
D23: JP1.1, JP2.1
GND: C1.2, C2.2, C9.2, C27.2, C28.2, C29.2, C30.2, J3.7, JP35.1, JP35.2, JP36.1, JP36.2, JP36.3, JP36.4, JP36.5, JP36.6, JP36.7, JP36.8, JP36.9, JP36.10, JP39.1, JP39.2, JP39.3, JP39.4, JP39.5, JP39.6, JP39.7, JP39.8, JP39.9, JP39.10, JP39.11, JP39.12, JP39.13, JP39.14, JP39.15, POWER.4, POWER.5, R19.1, R21.1, S1.1, S1.2, SL3.7, SLP.4, SLP.5, U$1.3, U$1.7, U$2.3, U$2.7, U$6.PIN1 (NA1), U$6.PIN2 (NA2), U$6.PIN3 (E2), U$6.PIN4 (VSS), U$7.PIN2 (GND), U$8.PIN2 (GND)
unnamed: LED1.A, R1.2
unnamed: LED1.C, RED.1
unnamed: LED2.A, R2.2
unnamed: GREEN.1, LED2.C
unnamed: R19.2, U$7.PIN8 (RS)
unnamed: JP4.1, JP7.1
unnamed: JP4.2, JP7.2
unnamed: JP5.1, JP8.1
unnamed: JP5.2, JP8.2
unnamed: JP6.1, JP9.1
unnamed: JP6.2, JP9.2
unnamed: JP12.1, JP15.1
unnamed: JP12.2, JP15.2
unnamed: JP13.1, JP16.1
unnamed: JP13.2, JP16.2
unnamed: JP14.1, JP17.1
unnamed: JP14.2, JP17.2
unnamed: JP20.1, JP23.1
unnamed: JP20.2, JP23.2
unnamed: JP21.1, JP24.1
unnamed: JP21.2, JP24.2
unnamed: JP22.1, JP25.1
unnamed: JP22.2, JP25.2
unnamed: JP28.1, JP29.1
unnamed: JP28.2, JP29.2
unnamed: JP32.1, JP33.1
unnamed: C28.1, R20.1, SJ2.2
unnamed: R20.2, SJ1.2
unnamed: R21.2, U$8.PIN8 (RS)
unnamed: C30.1, R22.1, SJ4.2
unnamed: R22.2, SJ3.2
RESET: POWER.1, S1.3, S1.4, SLP.1
SCL1: J3.10, SL3.10
SDA1: J3.9, SL3.9
VIN: POWER.6, SLP.6

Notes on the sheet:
Prototyping Area
Practical Arduino ProtoShield Mega
Revision 2.0
www.practicalarduino.com
Document Number:
1-010

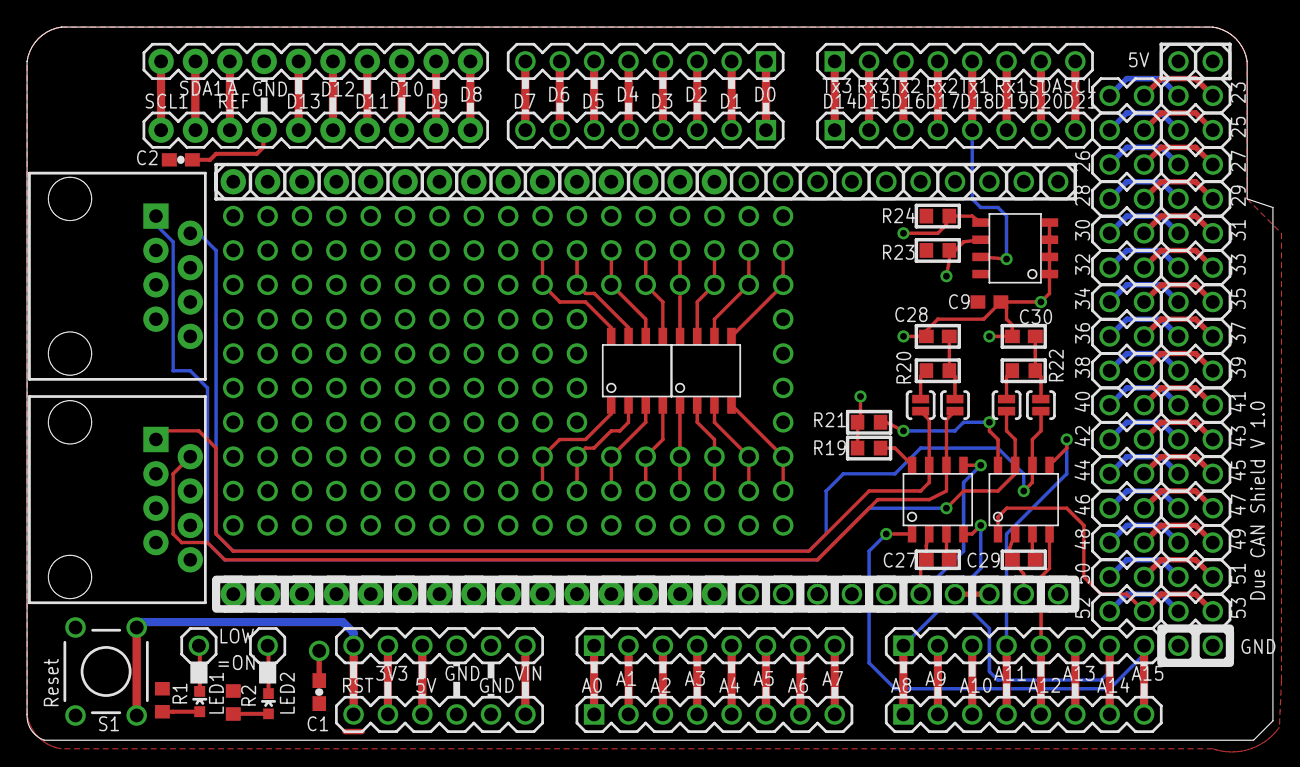
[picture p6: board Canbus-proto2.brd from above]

Board: 2 copper layers, 92.1 x 52.7 mm, 81 parts (0 on the bottom side), 92 nets.

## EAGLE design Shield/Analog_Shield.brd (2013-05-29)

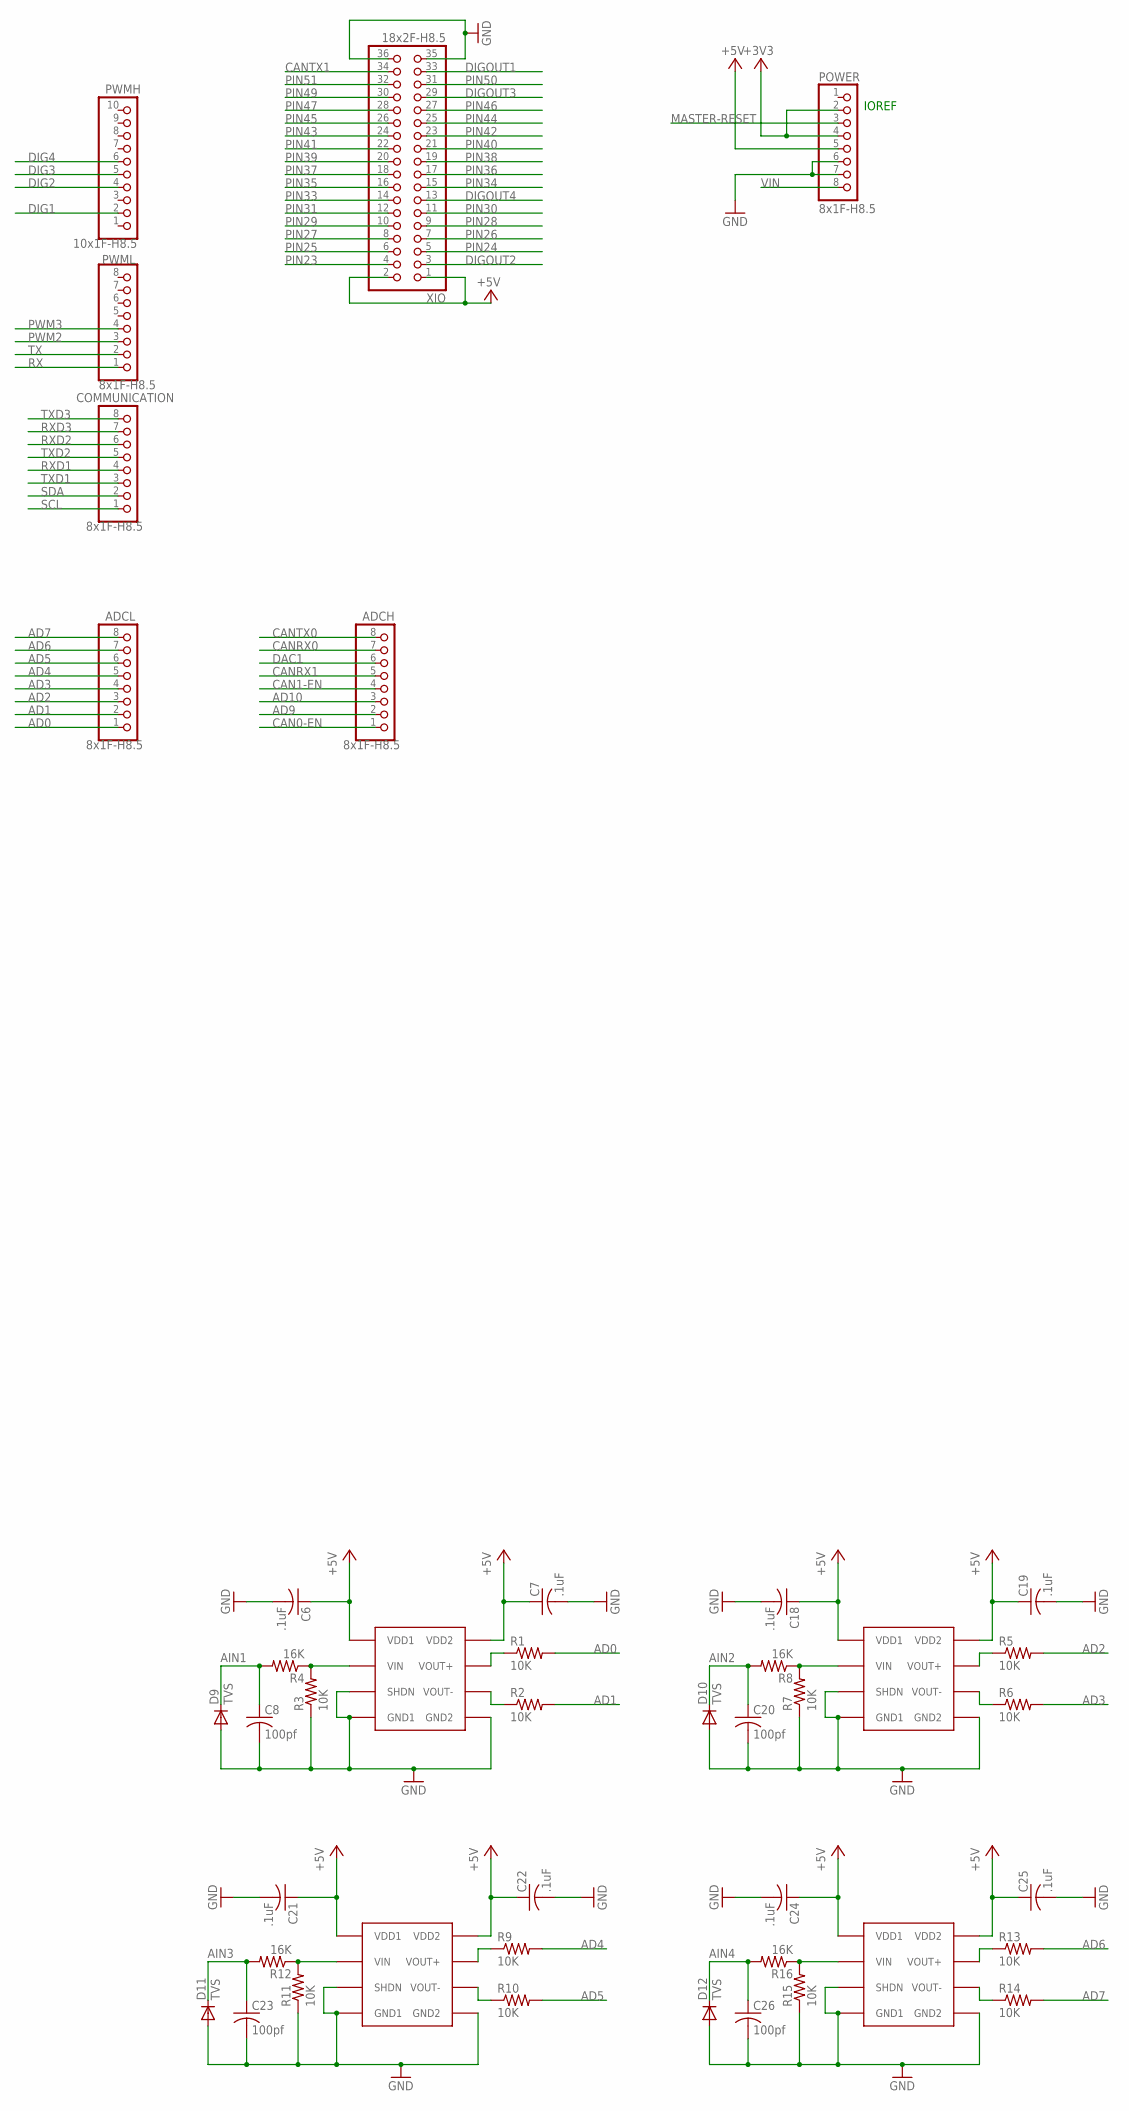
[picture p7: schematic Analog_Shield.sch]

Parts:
ADCH: 8x1F-H8.5; 1X08
ADCL: 8x1F-H8.5; 1X08
C6, C7, C18, C19, C21, C22, C24, C25: .1uF; C0603
C8, C20, C23, C26: 100pf; C0603
COMMUNICATION: 8x1F-H8.5; 1X08
D9, D10, D11, D12: TVS; SOD-323
POWER: 8x1F-H8.5; 1X08
PWMH: 10x1F-H8.5; 1X10
PWML: 8x1F-H8.5; 1X08
R1, R2, R3, R5, R6, R7, R9, R10, R11, R13, R14, R15: 10K; R0603
R4, R8, R12, R16: 16K; R0603
U$1, U$10, U$11, U$12: ACPL-C87A-000E; SO8-WIDE
XIO: 18x2F-H8.5; 2X18

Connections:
+3V3: POWER.2, POWER.4
+5V: C6.1, C7.1, C18.1, C19.1, C21.1, C22.1, C24.1, C25.1, POWER.5, U$1.1 (VDD1), U$1.8 (VDD2), U$10.1 (VDD1), U$10.8 (VDD2), U$11.1 (VDD1), U$11.8 (VDD2), U$12.1 (VDD1), U$12.8 (VDD2), XIO.1, XIO.2
AD0: ADCL.1, R1.2
AD1: ADCL.2, R2.2
AD2: ADCL.3, R5.2
AD3: ADCL.4, R6.2
AD4: ADCL.5, R9.2
AD5: ADCL.6, R10.2
AD6: ADCL.7, R13.2
AD7: ADCL.8, R14.2
AD9: ADCH.2
AD10: ADCH.3
AIN1: C8.1, D9.1 (C), R4.2
AIN2: C20.1, D10.1 (C), R8.2
AIN3: C23.1, D11.1 (C), R12.2
AIN4: C26.1, D12.1 (C), R16.2
CAN0-EN: ADCH.1
CAN1-EN: ADCH.4
CANRX0: ADCH.7
CANRX1: ADCH.5
CANTX0: ADCH.8
CANTX1: XIO.34
DAC1: ADCH.6
DIG1: PWMH.2
DIG2: PWMH.4
DIG3: PWMH.5
DIG4: PWMH.6
DIGOUT1: XIO.33
DIGOUT2: XIO.3
DIGOUT3: XIO.29
DIGOUT4: XIO.13
GND: C6.2, C7.2, C8.2, C18.2, C19.2, C20.2, C21.2, C22.2, C23.2, C24.2, C25.2, C26.2, D9.2 (A), D10.2 (A), D11.2 (A), D12.2 (A), POWER.6, POWER.7, R3.1, R7.1, R11.1, R15.1, U$1.3 (SHDN), U$1.4 (GND1), U$1.5 (GND2), U$10.3 (SHDN), U$10.4 (GND1), U$10.5 (GND2), U$11.3 (SHDN), U$11.4 (GND1), U$11.5 (GND2), U$12.3 (SHDN), U$12.4 (GND1), U$12.5 (GND2), XIO.35, XIO.36
MASTER-RESET: POWER.3
unnamed: R1.1, U$1.7 (VOUT+)
unnamed: R2.1, U$1.6 (VOUT-)
unnamed: R3.2, R4.1, U$1.2 (VIN)
unnamed: R7.2, R8.1, U$10.2 (VIN)
unnamed: R5.1, U$10.7 (VOUT+)
unnamed: R6.1, U$10.6 (VOUT-)
unnamed: R11.2, R12.1, U$11.2 (VIN)
unnamed: R9.1, U$11.7 (VOUT+)
unnamed: R10.1, U$11.6 (VOUT-)
unnamed: R15.2, R16.1, U$12.2 (VIN)
unnamed: R13.1, U$12.7 (VOUT+)
unnamed: R14.1, U$12.6 (VOUT-)
PIN23: XIO.4
PIN24: XIO.5
PIN25: XIO.6
PIN26: XIO.7
PIN27: XIO.8
PIN28: XIO.9
PIN29: XIO.10
PIN30: XIO.11
PIN31: XIO.12
PIN33: XIO.14
PIN34: XIO.15
PIN35: XIO.16
PIN36: XIO.17
PIN37: XIO.18
PIN38: XIO.19
PIN39: XIO.20
PIN40: XIO.21
PIN41: XIO.22
PIN42: XIO.23
PIN43: XIO.24
PIN44: XIO.25
PIN45: XIO.26
PIN46: XIO.27
PIN47: XIO.28
PIN49: XIO.30
PIN50: XIO.31
PIN51: XIO.32
PWM2: PWML.3
PWM3: PWML.4
RX: PWML.1
RXD1: COMMUNICATION.4
RXD2: COMMUNICATION.6
RXD3: COMMUNICATION.7
SCL: COMMUNICATION.1
SDA: COMMUNICATION.2
TX: PWML.2
TXD1: COMMUNICATION.3
TXD2: COMMUNICATION.5
TXD3: COMMUNICATION.8
VIN: POWER.8

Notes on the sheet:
IOREF

Board: 2 copper layers, 43 parts (0 on the bottom side), 27 nets, no tracks yet.

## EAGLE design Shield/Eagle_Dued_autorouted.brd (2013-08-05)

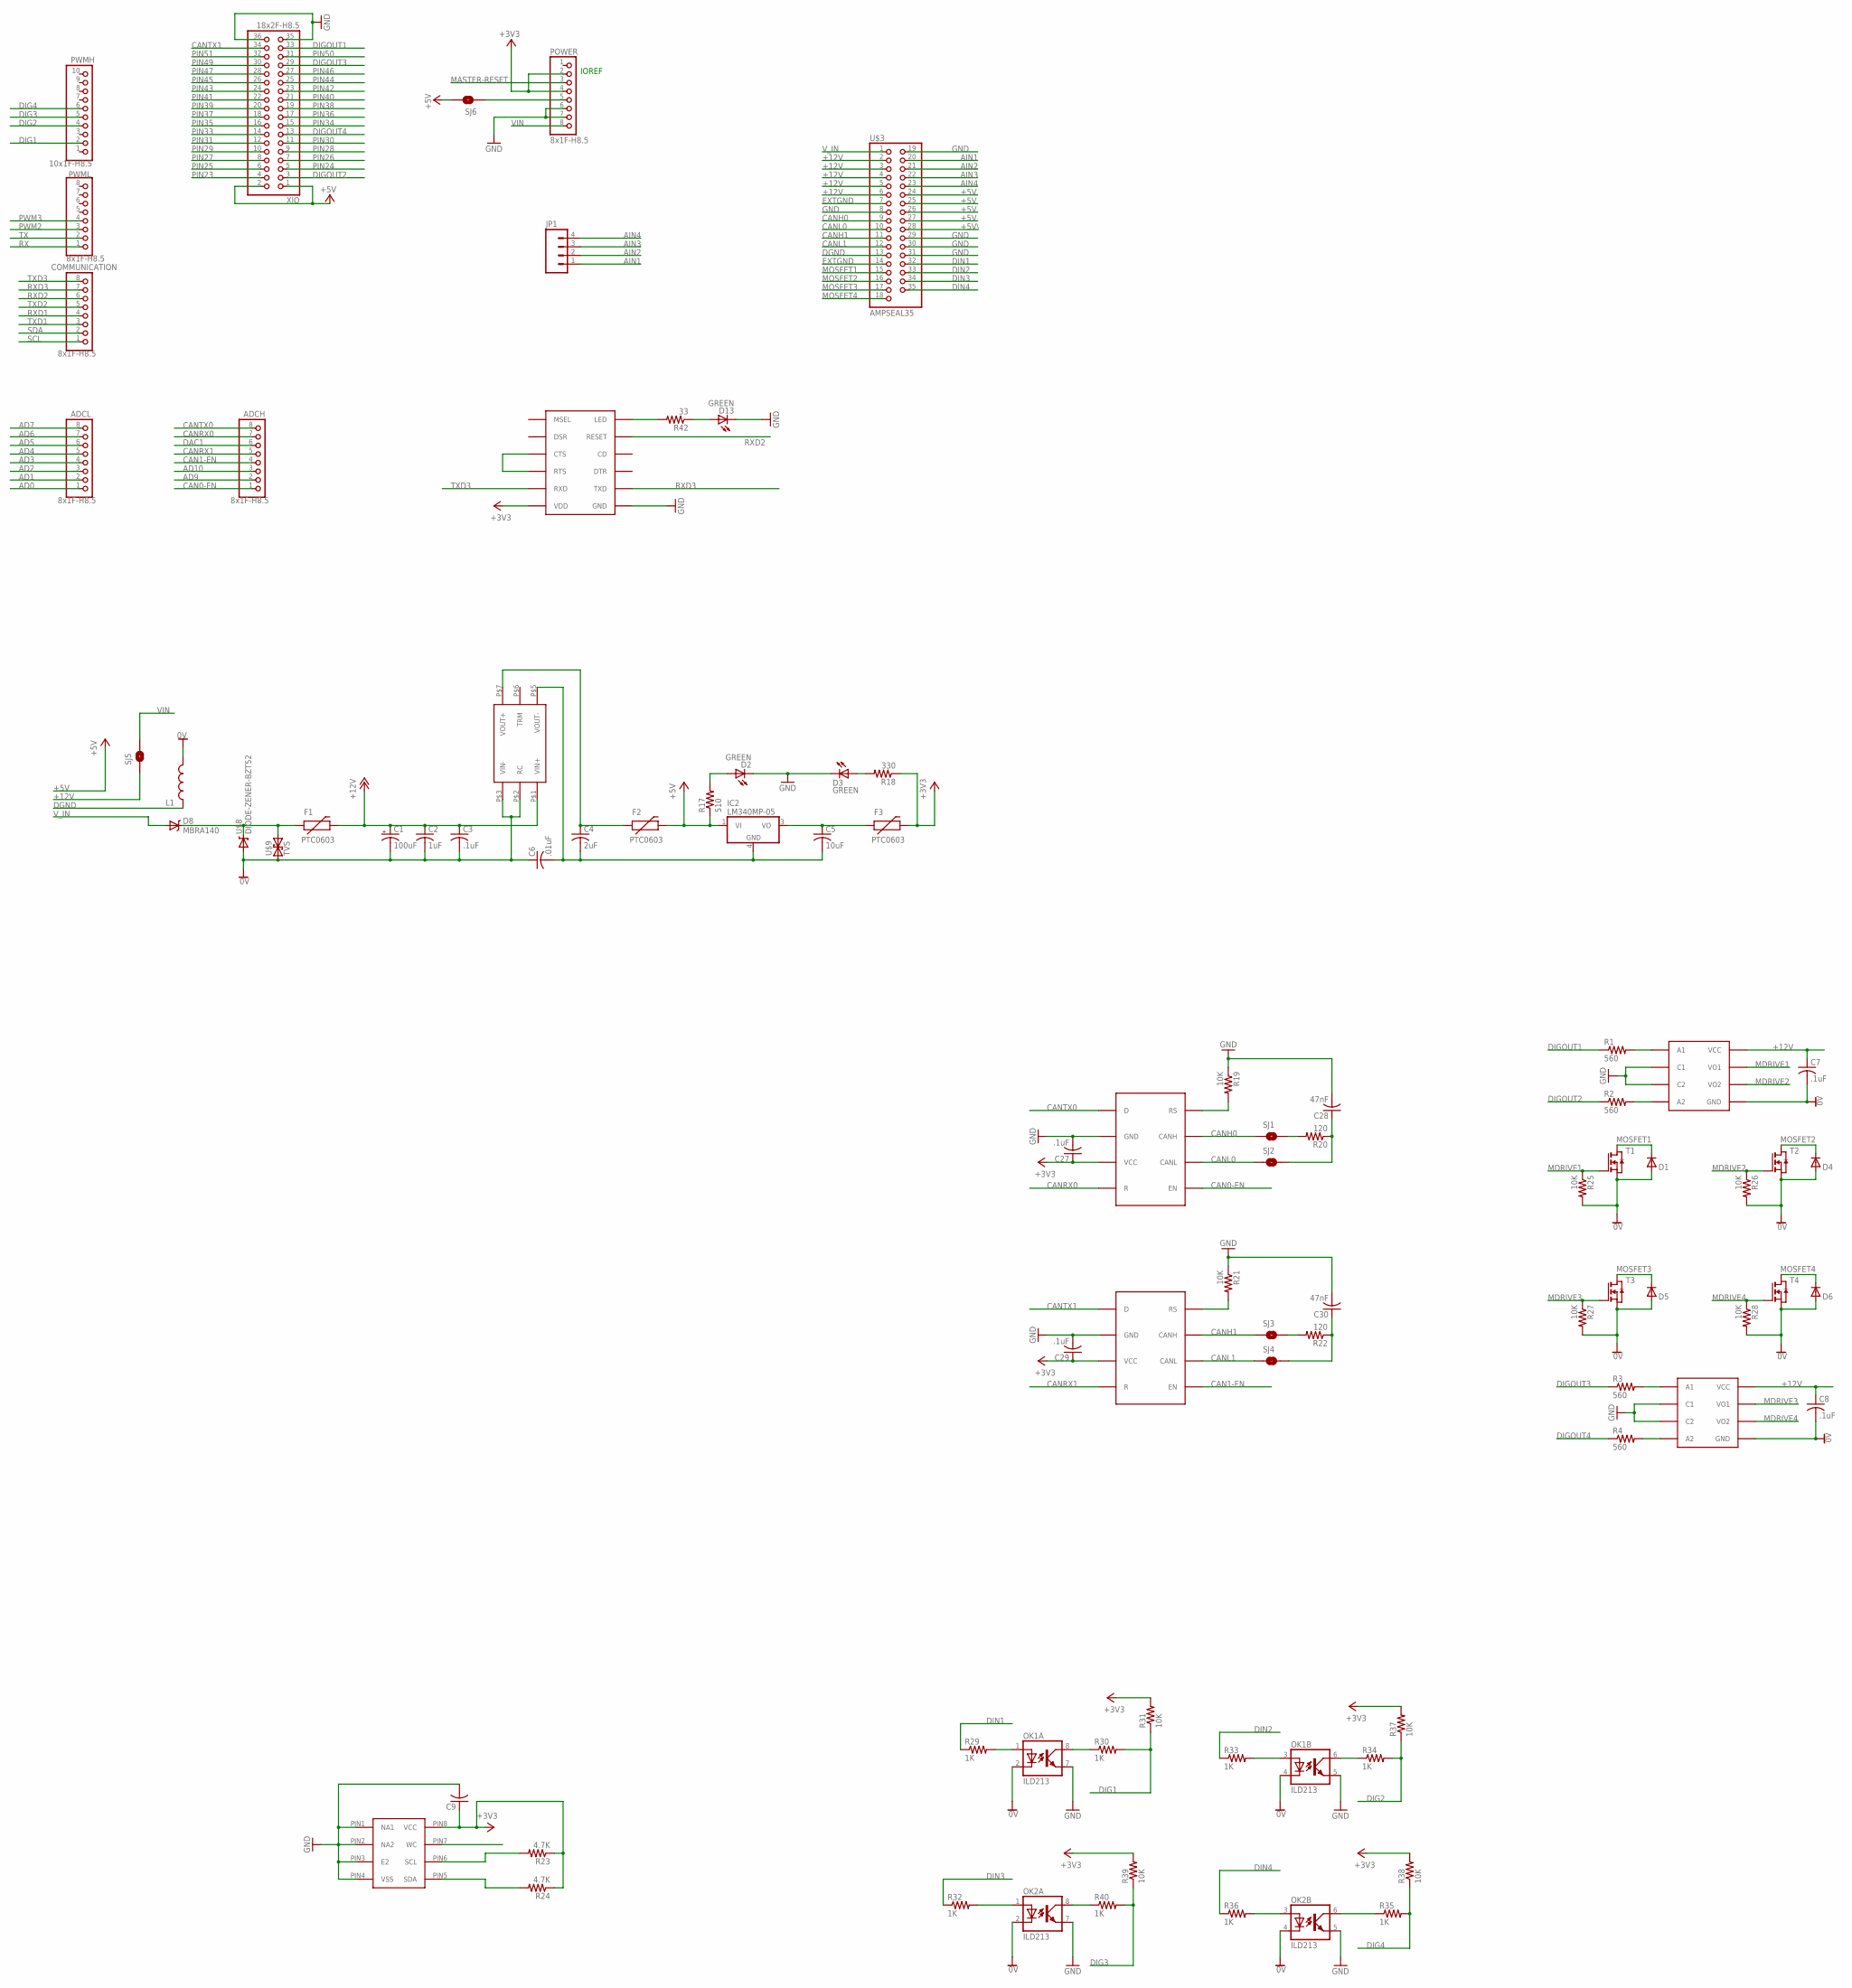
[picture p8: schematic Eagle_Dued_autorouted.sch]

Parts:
ADCH: 8x1F-H8.5; 1X08
ADCL: 8x1F-H8.5; 1X08
C1: 100uF; E2,5-6
C2: 1uF; C1206
C3, C7, C8: .1uF; C1206
C4: 2uF; C0805
C5: 10uF; C1206
C6: .01uF; C1206
C9: C-USC0603; C0603
C27, C29: .1uF; C0603
C28, C30: 47nF; C0603
COMMUNICATION: 8x1F-H8.5; 1X08
D1, D4, D5, D6: MBR0520LT; SOD123
D2, D3, D13: GREEN; LED-0603
D8: MBRA140; SMA-DIODE
F1, F2, F3: PTC0603; 0603
IC2: LM340MP-05; SOT223
JP1: M04POLAR; MOLEX-1X4
L1: INDUCTOR1206H*; INDUCTOR-1206
OK1, OK2: ILD213; SOIC08
POWER: 8x1F-H8.5; 1X08
PWMH: 10x1F-H8.5; 1X10
PWML: 8x1F-H8.5; 1X08
R1, R2, R3, R4: 560; R0603
R17: 510; R0603
R18: 330; R0603
R19, R21, R25, R26, R27, R28, R31, R37, R38, R39: 10K; R0603
R20, R22: 120; R0603
R23, R24: 4.7K; R0603
R29, R30, R32, R33, R34, R35, R36, R40: 1K; R0603
R42: 33; R0603
SJ1, SJ2, SJ3, SJ4, SJ5, SJ6: SOLDERJUMPERNO; SJ_2S-NO
T1, T2, T3, T4: NMOSSOT223; SOT223
U$1: CC3-E
U$2, U$6: SN65HVD234; SOIC8
U$3: AMPSEAL35
U$4: MINIWIFI
U$5: M24M02-DRMN6TP; SOIC8
U$7, U$10: SFH6731; DIP8
U$8: DIODE-ZENER-BZT52; SOD-323
U$9: TVS; SMA-DIODE
XIO: 18x2F-H8.5; 2X18

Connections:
0V: C7.2, C8.2, OK1.2 (C), OK1.4 (C), OK2.2 (C), OK2.4 (C), U$7.5 (GND), U$10.5 (GND)
+3V3: C9.1, C27.1, C29.1, F3.2, POWER.2, POWER.4, R18.1, R23.1, R24.1, R31.2, R37.2, R38.2, R39.2, U$2.PIN3 (VCC), U$4.P$1 (VDD), U$5.PIN8 (VCC), U$6.PIN3 (VCC)
+5V: F2.2, IC2.1 (VI), R17.1, SJ6.2, U$3.24, U$3.25, U$3.26, U$3.27, XIO.1, XIO.2
+5V\: U$3.28
+12V: C1.+, C2.1, C3.1, C7.1, C8.1, F1.2, SJ5.1, U$1.P$1 (VIN+), U$3.2, U$3.3, U$3.4, U$3.5, U$3.6, U$7.8 (VCC), U$10.8 (VCC)
AD0: ADCL.1
AD1: ADCL.2
AD2: ADCL.3
AD3: ADCL.4
AD4: ADCL.5
AD5: ADCL.6
AD6: ADCL.7
AD7: ADCL.8
AD9: ADCH.2
AD10: ADCH.3
AIN1: JP1.1, U$3.20
AIN2: JP1.2, U$3.21
AIN3: JP1.3, U$3.22
AIN4: JP1.4, U$3.23
CAN0-EN: ADCH.1, U$6.PIN5 (EN)
CAN1-EN: ADCH.4, U$2.PIN5 (EN)
CANH0: SJ1.1, U$3.9, U$6.PIN7 (CANH)
CANH1: SJ3.1, U$2.PIN7 (CANH), U$3.11
CANL0: SJ2.1, U$3.10, U$6.PIN6 (CANL)
CANL1: SJ4.1, U$2.PIN6 (CANL), U$3.12
CANRX0: ADCH.7, U$6.PIN4 (R)
CANRX1: ADCH.5, U$2.PIN4 (R)
CANTX0: ADCH.8, U$6.PIN1 (D)
CANTX1: U$2.PIN1 (D), XIO.34
DAC1: ADCH.6
DGND: L1.P$1 (1), U$3.13
DIG1: PWMH.2, R30.2, R31.1
DIG2: PWMH.4, R34.2, R37.1
DIG3: PWMH.5, R39.1, R40.2
DIG4: PWMH.6, R35.2, R38.1
DIGOUT1: R1.1, XIO.33
DIGOUT2: R2.1, XIO.3
DIGOUT3: R3.1, XIO.29
DIGOUT4: R4.1, XIO.13
DIN1: R29.1, U$3.32
DIN2: R33.1, U$3.33
DIN3: R32.1, U$3.34
DIN4: R36.1, U$3.35
EXTGND: C1.-, C2.2, C3.2, C6.1, D1.A, D4.A, D5.A, D6.A, L1.P$2 (2), R25.2, R26.2, R27.2, R28.2, T1.3 (S), T2.3 (S), T3.3 (S), T4.3 (S), U$1.P$2 (RC), U$1.P$3 (VIN-), U$3.7, U$3.14, U$8.2 (A), U$9.A (1)
GND: C4.2, C5.2, C6.2, C9.2, C27.2, C28.2, C29.2, C30.2, D2.C, D3.C, D13.C, IC2.4 (GND), OK1.5 (EMIT), OK1.7 (EMIT), OK2.5 (EMIT), OK2.7 (EMIT), POWER.6, POWER.7, R19.1, R21.1, U$1.P$5 (VOUT-), U$2.PIN2 (GND), U$3.8, U$3.19, U$3.29, U$3.30, U$3.31, U$4.P$2 (GND), U$5.PIN1 (NA1), U$5.PIN2 (NA2), U$5.PIN3 (E2), U$5.PIN4 (VSS), U$6.PIN2 (GND), U$7.2 (C1), U$7.3 (C2), U$10.2 (C1), U$10.3 (C2), XIO.35, XIO.36
MASTER-RESET: POWER.3
MDRIVE1: R25.1, T1.1 (G), U$10.7 (VO1)
MDRIVE2: R26.1, T2.1 (G), U$10.6 (VO2)
MDRIVE3: R27.1, T3.1 (G), U$7.7 (VO1)
MDRIVE4: R28.1, T4.1 (G), U$7.6 (VO2)
MOSFET1: D1.C, T1.2 (D), T1.4 (D), U$3.15
MOSFET2: D4.C, T2.2 (D), T2.4 (D), U$3.16
MOSFET3: D5.C, T3.2 (D), T3.4 (D), U$3.17
MOSFET4: D6.C, T4.2 (D), T4.4 (D), U$3.18
unnamed: POWER.5, SJ6.1
unnamed: U$4.P$5 (RTS), U$4.P$7 (CTS)
unnamed: D8.C, F1.1, U$8.1 (C), U$9.C (2)
unnamed: R42.2, U$4.P$12 (LED)
unnamed: R3.2, U$7.1 (A1)
unnamed: C4.1, F2.1, U$1.P$7 (VOUT+)
unnamed: R1.2, U$10.1 (A1)
unnamed: C5.1, F3.1, IC2.3 (VO)
unnamed: D13.A, R42.1
unnamed: R2.2, U$10.4 (A2)
unnamed: R4.2, U$7.4 (A2)
unnamed: D2.A, R17.2
unnamed: R19.2, U$6.PIN8 (RS)
unnamed: D3.A, R18.2
unnamed: C28.1, R20.1, SJ2.2
unnamed: R20.2, SJ1.2
unnamed: R21.2, U$2.PIN8 (RS)
unnamed: C30.1, R22.1, SJ4.2
unnamed: R22.2, SJ3.2
unnamed: OK1.1 (A), R29.2
unnamed: OK1.3 (A), R33.2
unnamed: OK1.8 (COL), R30.1
unnamed: OK1.6 (COL), R34.1
unnamed: OK2.6 (COL), R35.1
unnamed: OK2.8 (COL), R40.1
unnamed: OK2.1 (A), R32.2
unnamed: OK2.3 (A), R36.2
PIN23: XIO.4
PIN24: XIO.5
PIN25: XIO.6
PIN26: XIO.7
PIN27: XIO.8
PIN28: XIO.9
PIN29: XIO.10
PIN30: XIO.11
PIN31: XIO.12
PIN33: XIO.14
PIN34: XIO.15
PIN35: XIO.16
PIN36: XIO.17
PIN37: XIO.18
PIN38: XIO.19
PIN39: XIO.20
PIN40: XIO.21
PIN41: XIO.22
PIN42: XIO.23
PIN43: XIO.24
PIN44: XIO.25
PIN45: XIO.26
PIN46: XIO.27
PIN47: XIO.28
PIN49: XIO.30
PIN50: XIO.31
PIN51: XIO.32
PWM2: PWML.3
PWM3: PWML.4
RX: PWML.1
RXD1: COMMUNICATION.4, U$5.PIN7 (WC)
RXD2: COMMUNICATION.6, U$4.P$10 (RESET)
RXD3: COMMUNICATION.7, U$4.P$4 (TXD)
SCL: COMMUNICATION.1, R23.2, U$5.PIN6 (SCL)
SDA: COMMUNICATION.2, R24.2, U$5.PIN5 (SDA)
TX: PWML.2
TXD1: COMMUNICATION.3
TXD2: COMMUNICATION.5
TXD3: COMMUNICATION.8, U$4.P$3 (RXD)
VIN: POWER.8, SJ5.2
V_IN: D8.A, U$3.1

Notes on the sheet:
IOREF

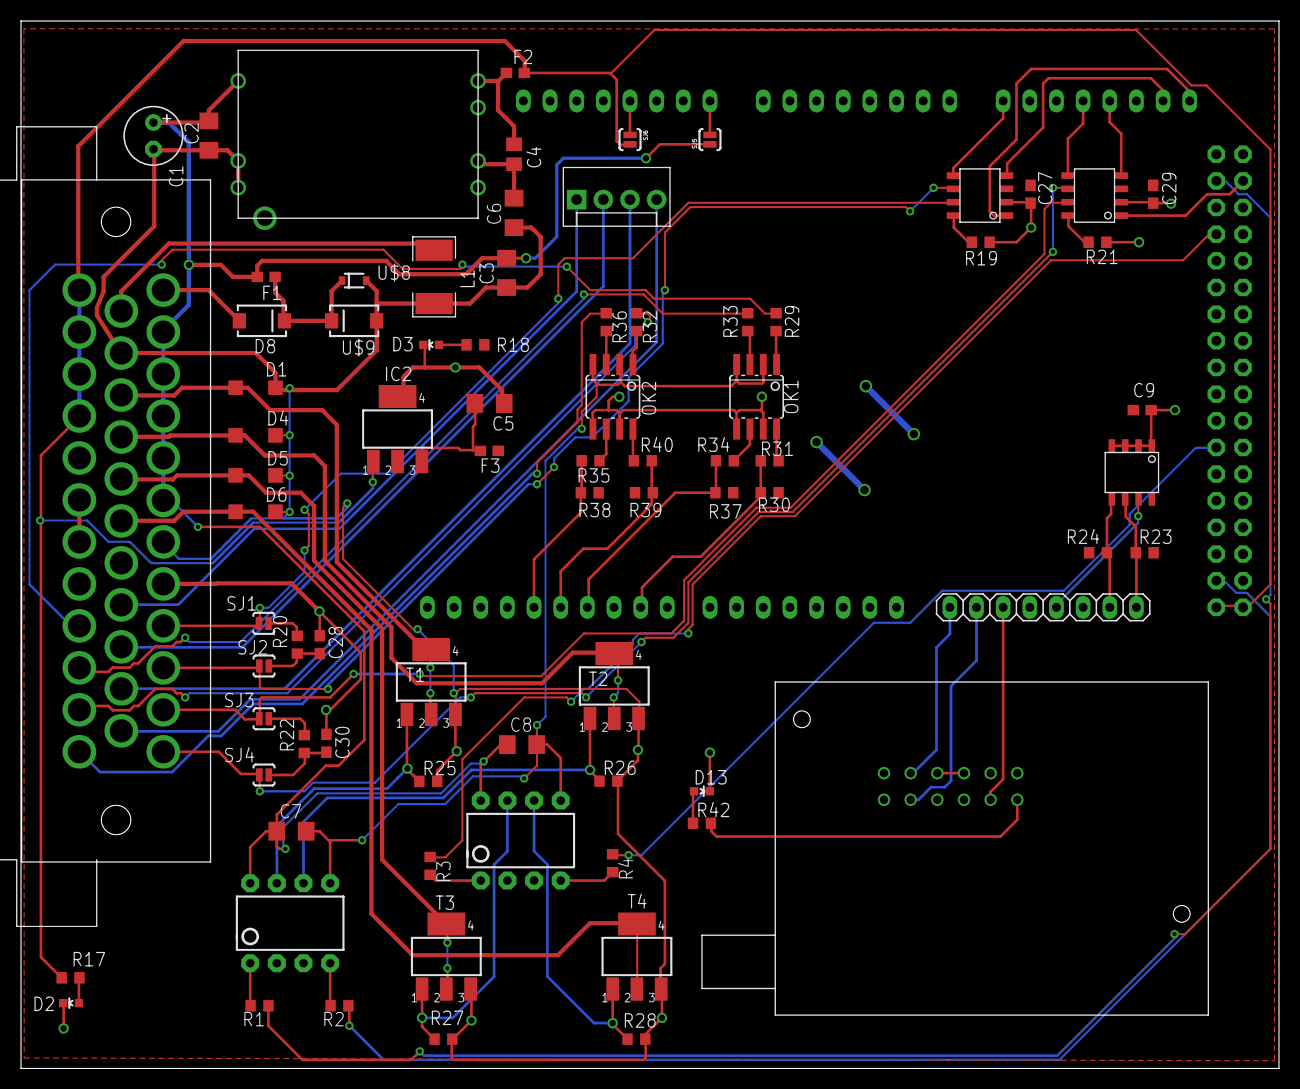
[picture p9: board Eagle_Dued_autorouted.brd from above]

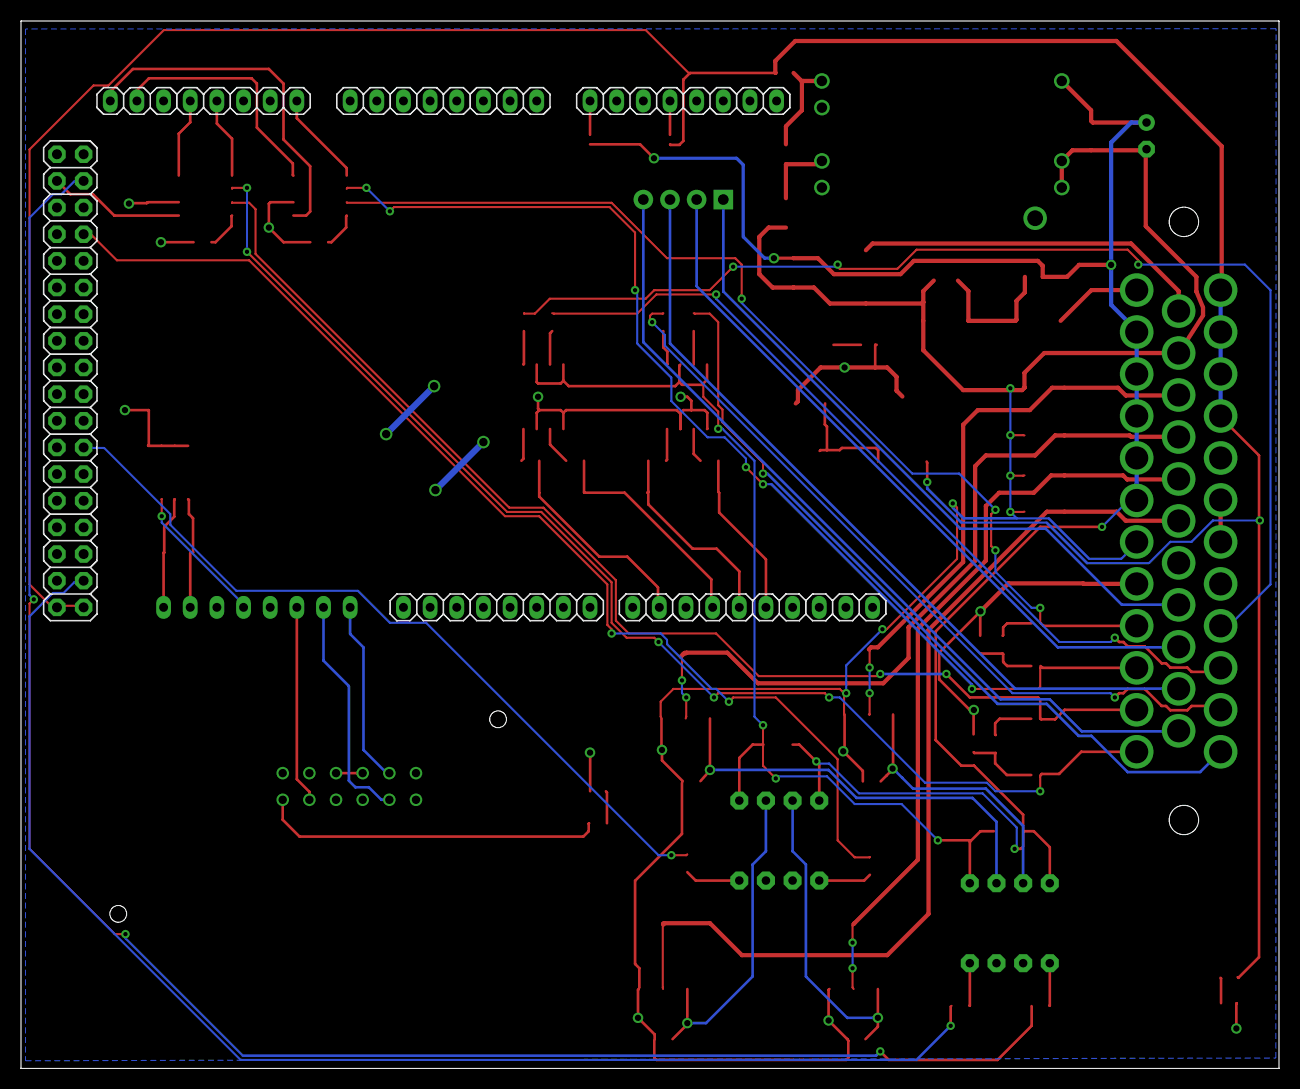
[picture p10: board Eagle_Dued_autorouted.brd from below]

Board: 2 copper layers, 119.9 x 99.8 mm, 85 parts (6 on the bottom side), 76 nets.

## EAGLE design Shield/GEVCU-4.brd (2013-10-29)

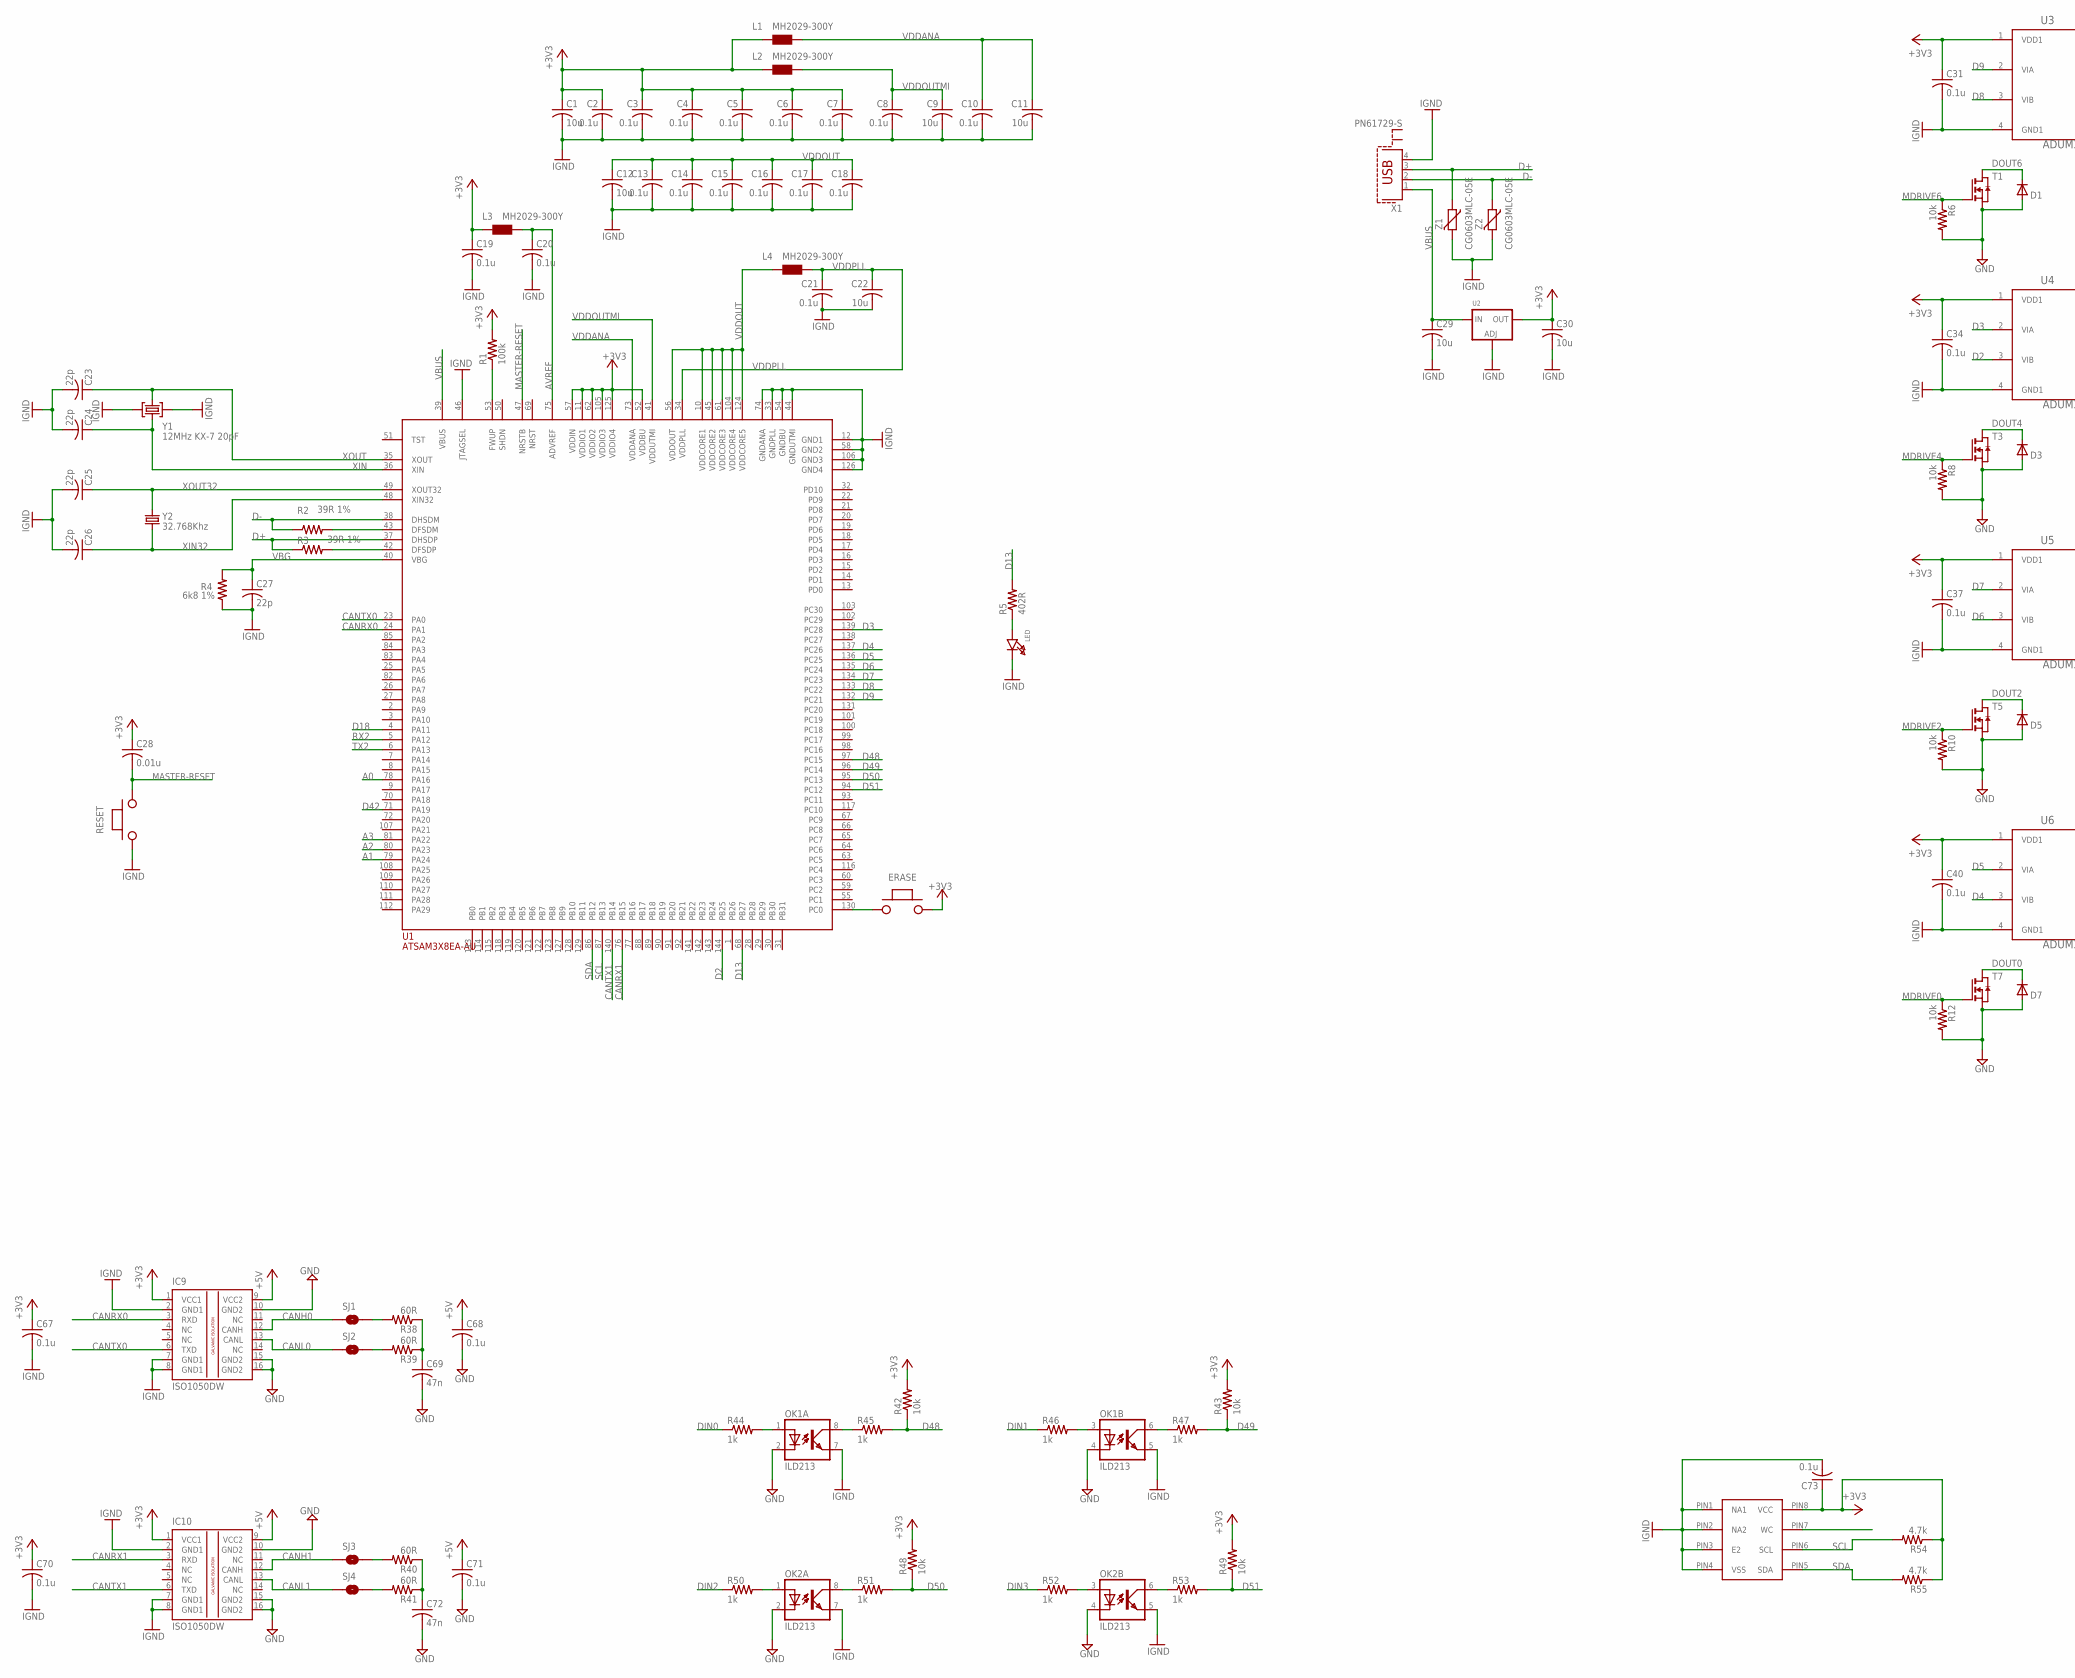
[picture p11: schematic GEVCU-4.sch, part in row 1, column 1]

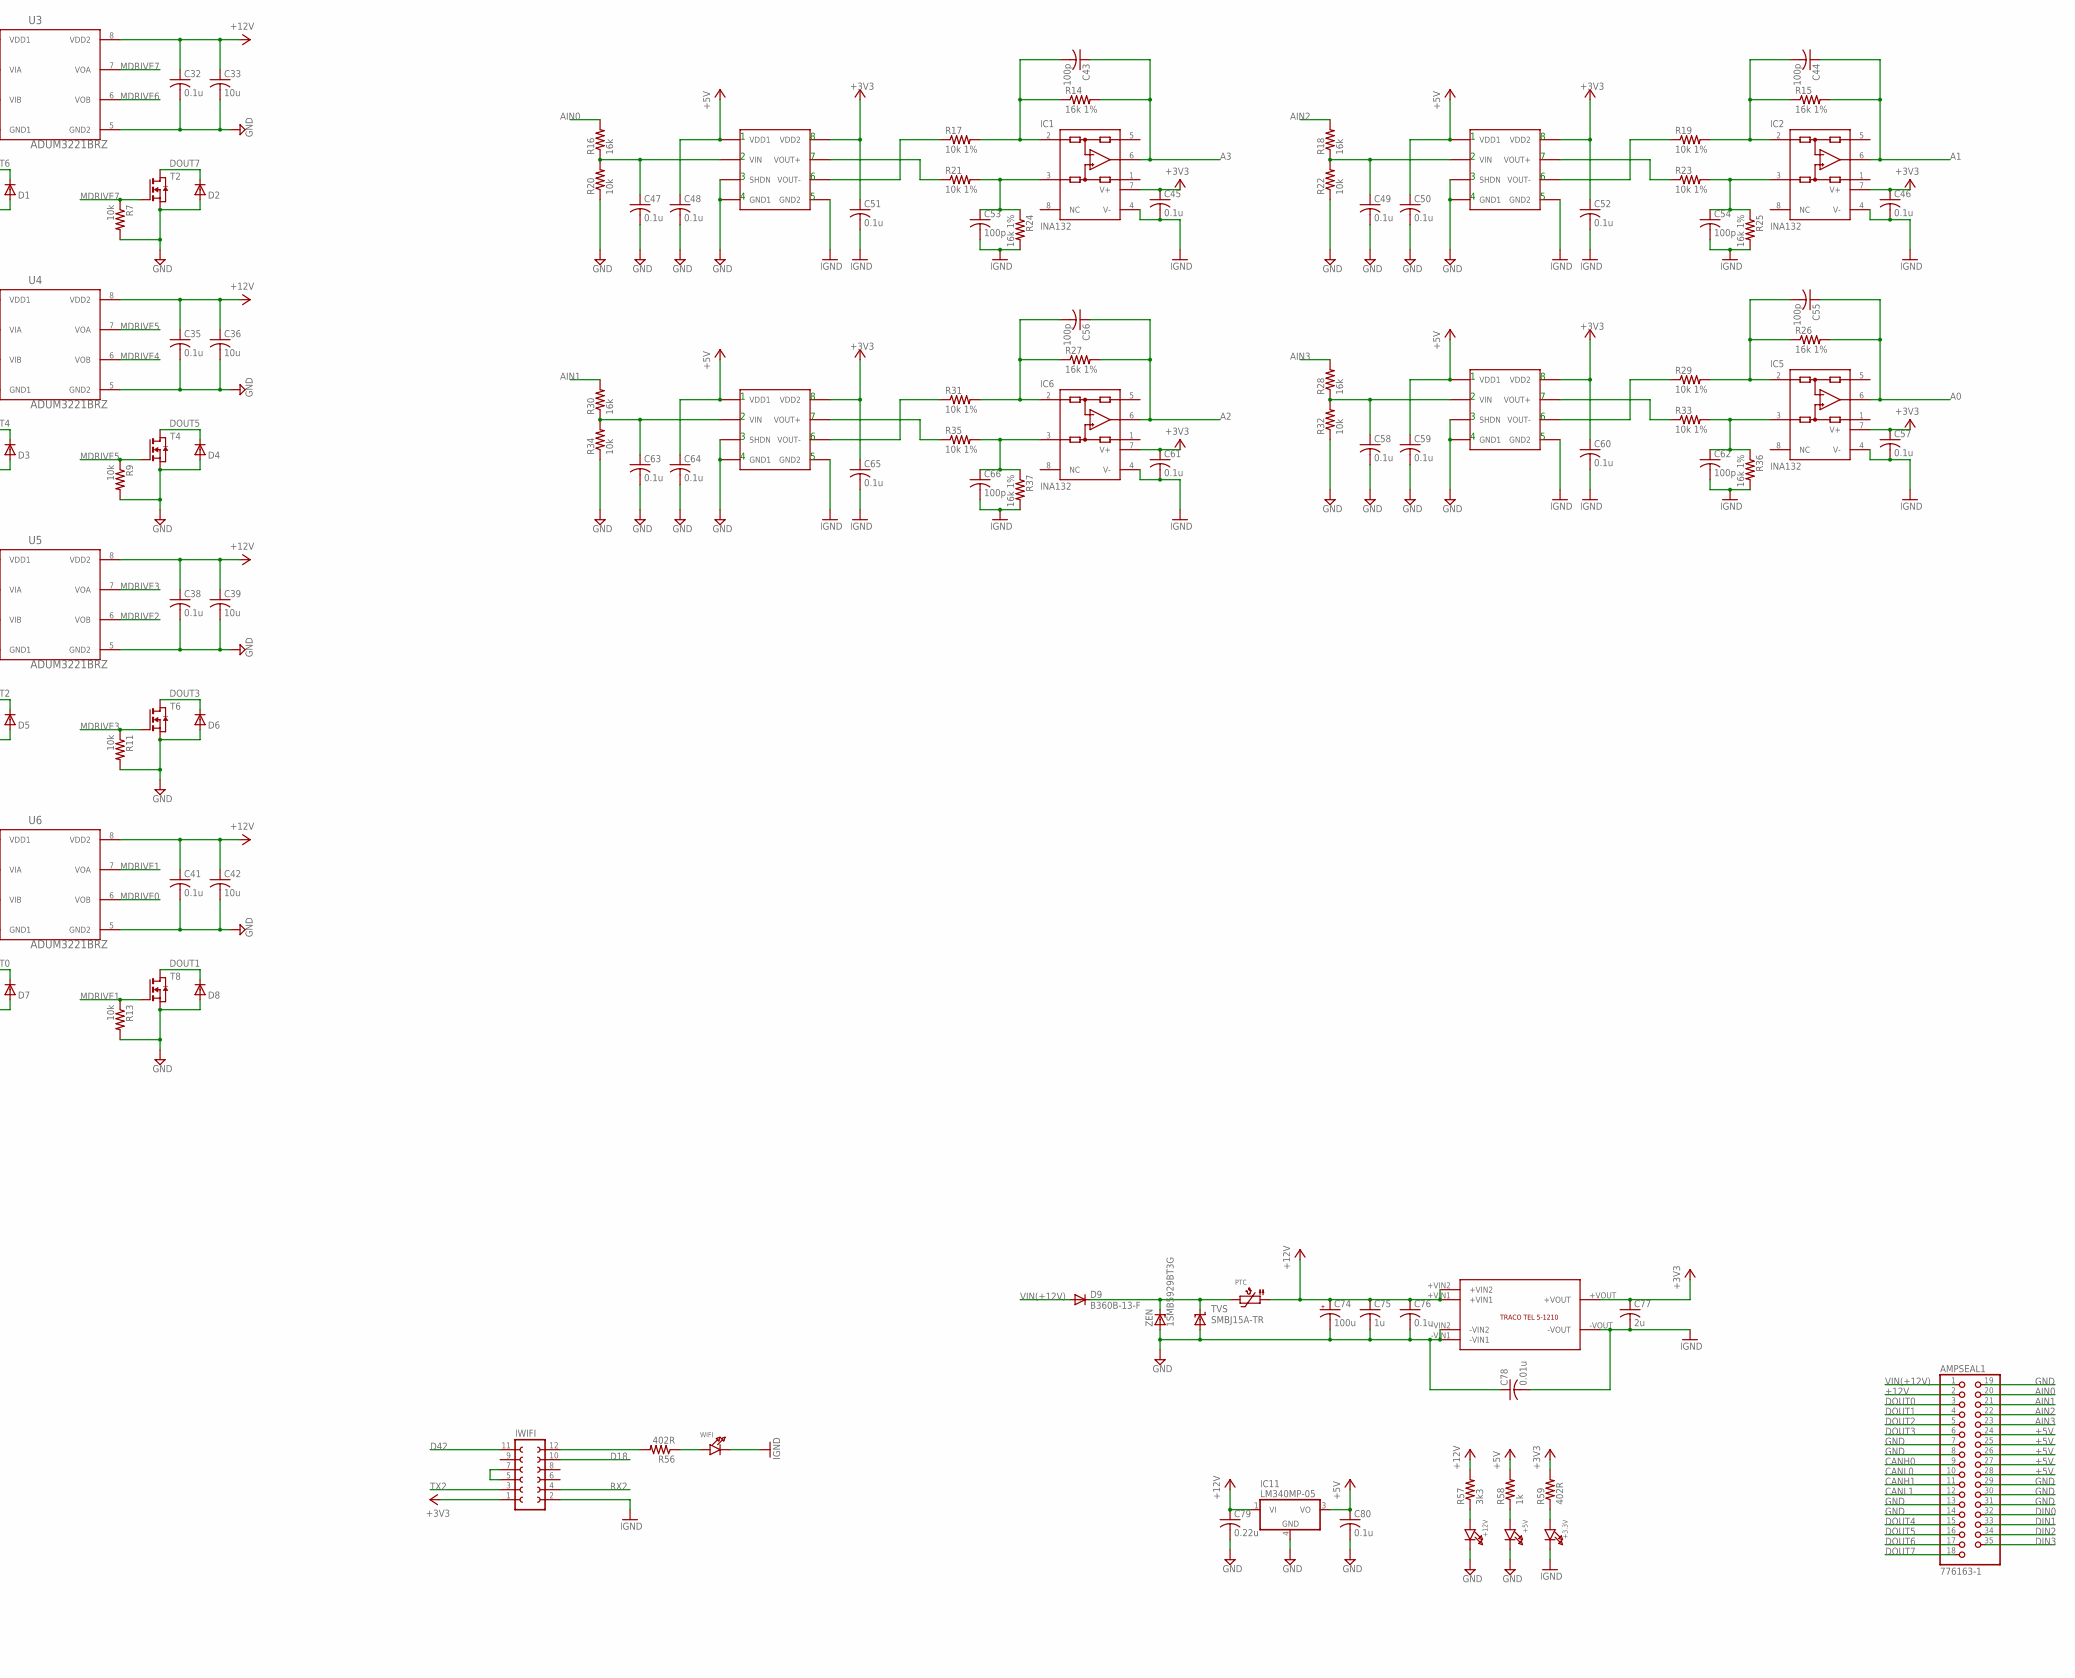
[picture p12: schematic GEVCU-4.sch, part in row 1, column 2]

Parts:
+3.3V, +5V, +12V: LED0805; CHIPLED_0805
AMPSEAL1: 776163-1; AMPSEAL35
C1, C9, C11, C12, C22, C29, C30, C33, C36, C39, C42: 10u; C0805
C2, C3, C4, C5, C6, C7, C8, C10, C13, C14, C15, C16, C17, C18, C19, C20, C21, C31, C32, C34, C35, C37, C38, C40, C41, C45, C46, C47, C49, C51, C52, C57, C58, C60, C61, C63, C65, C67, C68, C70, C71, C73, C76, C80: 0.1u; C0805
C23, C24: 22p; C1206
C25, C26, C27: 22p; C0805
C28: 0.01u; C0805
C43, C44, C53, C54, C55, C56, C62, C66: 100p; C0805
C48, C50, C59, C64: 0.1u; C1206
C69, C72: 47n; C0805
C74: 100u; E2,5-6
C75: 1u; C0805
C77: 2u; C0805
C78: 0.01u; C1812
C79: 0.22u; C0805
D1, D2, D3, D4, D5, D6, D7, D8: MBR0520LT; SOD123
D9: B360B-13-F; SMB
ERASE: PUCHBUTTON
IC1, IC2, IC5, IC6: INA132; SO08
IC3, IC4, IC7, IC8: CK_CUSTOM_ACPL-C87A-000E; CK_CUSTOM_SO8-WIDE
IC9, IC10: ISO1050DW; DUB-R-PDSO-G8
IC11: LM340MP-05; SOT223
IWIFI: FE06-2
L1, L2, L3, L4: MH2029-300Y; 0805
LED: LED0805; CHIPLED_0805
OK1, OK2: ILD213; SOIC08
PTC: PTC1812
R1: 100k; R0805
R2, R3: 39R 1%; R0805
R4: 6k8 1%; R0805
R5, R56, R59: 402R; R0805
R6, R7, R8, R9, R10, R11, R12, R13, R20, R22, R32, R34, R42, R43, R48, R49: 10k; R0805
R14, R15, R24, R25, R26, R27, R36, R37: 16k 1%; R0805
R16, R18, R28, R30: 16k; R0805
R17, R19, R21, R23, R29, R31, R33, R35: 10k 1%; R0805
R38, R39, R40, R41: 60R; R0805
R44, R45, R46, R47, R50, R51, R52, R53, R58: 1k; R0805
R54, R55: 4.7k; R0805
R57: 3k3; R0805
RESET: PUCHBUTTON
SJ1, SJ2, SJ3, SJ4: SOLDERJUMPERNO; SJ_2S-NO
T1, T2, T3, T4, T5, T6, T7, T8: NMOSSOT223; SOT223
TVS: SMBJ15A-TR; SMBJ
U1: ATSAM3X8EA-AU; LQFP144
U2: LM1117SOT223-WAVE; SOT223-W
U3, U4, U5, U6: ADUM3221BRZ; SOIC127P600X175-8N
U7: CK_CUSTOM_M24M02-DRMN6TP; CK_CUSTOM_SOIC8
U8: TRACO
WIFI: LED0805; CHIPLED_0805
X1: PN61729-S
Y1: 12MHz KX-7 20pF; CRYSTAL-3.2-2.5
Y2: 32.768Khz; RESONATOR_EPSON_FC_145
Z1, Z2: CG0603MLC-05E; CT/CN0603
ZEN: 1SMB5929BT3G; SMB

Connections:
+3V3: C1.1, C2.1, C3.1, C4.1, C5.1, C6.1, C7.1, C19.1, C28.1, C30.1, C31.1, C34.1, C37.1, C40.1, C45.1, C46.1, C51.1, C52.1, C57.1, C60.1, C61.1, C65.1, C67.1, C70.1, C73.1, C77.1, ERASE.P$2, IC1.7 (V+), IC2.7 (V+), IC3.8 (VDD2), IC4.8 (VDD2), IC5.7 (V+), IC6.7 (V+), IC7.8 (VDD2), IC8.8 (VDD2), IC9.1 (VCC1), IC10.1 (VCC1), IWIFI.1, L1.1, L2.1, L3.1, R1.2, R42.2, R43.2, R48.2, R49.2, R54.1, R55.1, R59.2, U1.11 (VDDIO1), U1.52 (VDDBU), U1.57 (VDDIN), U1.62 (VDDIO2), U1.105 (VDDIO3), U1.125 (VDDIO4), U2.2 (OUT), U3.1 (VDD1), U4.1 (VDD1), U5.1 (VDD1), U6.1 (VDD1), U7.PIN8 (VCC), U8.+VOUT
+5V: AMPSEAL1.24, AMPSEAL1.25, AMPSEAL1.26, AMPSEAL1.27, AMPSEAL1.28, C48.1, C50.1, C59.1, C64.1, C68.1, C71.1, C80.1, IC3.1 (VDD1), IC4.1 (VDD1), IC7.1 (VDD1), IC8.1 (VDD1), IC9.9 (VCC2), IC10.9 (VCC2), IC11.3 (VO), R58.2
+12V: AMPSEAL1.2, C32.1, C33.1, C35.1, C36.1, C38.1, C39.1, C41.1, C42.1, C74.+, C75.1, C76.1, C79.1, IC11.1 (VI), PTC.P$1 (1), R57.2, U3.8 (VDD2), U4.8 (VDD2), U5.8 (VDD2), U6.8 (VDD2), U8.+VIN1, U8.+VIN2
A0: C55.1, IC5.6 (OUT), R26.2, U1.78 (PA16)
A1: C44.1, IC2.6 (OUT), R15.2, U1.79 (PA24)
A2: C56.1, IC6.6 (OUT), R27.2, U1.80 (PA23)
A3: C43.1, IC1.6 (OUT), R14.2, U1.81 (PA22)
AIN0: AMPSEAL1.20, R16.2
AIN1: AMPSEAL1.21, R30.2
AIN2: AMPSEAL1.22, R18.2
AIN3: AMPSEAL1.23, R28.2
AVREF: C20.1, L3.2, U1.75 (ADVREF)
CANH0: AMPSEAL1.9, IC9.12 (CANH), SJ1.1
CANH1: AMPSEAL1.11, IC10.12 (CANH), SJ3.1
CANL0: AMPSEAL1.10, IC9.13 (CANL), SJ2.1
CANL1: AMPSEAL1.12, IC10.13 (CANL), SJ4.1
CANRX0: IC9.3 (RXD), U1.24 (PA1)
CANRX1: IC10.3 (RXD), U1.76 (PB15)
CANTX0: IC9.6 (TXD), U1.23 (PA0)
CANTX1: IC10.6 (TXD), U1.140 (PB14)
D2: U1.144 (PB25), U4.3 (VIB)
D3: U1.139 (PC28), U4.2 (VIA)
D4: U1.137 (PC26), U6.3 (VIB)
D5: U1.136 (PC25), U6.2 (VIA)
D6: U1.135 (PC24), U5.3 (VIB)
D7: U1.134 (PC23), U5.2 (VIA)
D8: U1.133 (PC22), U3.3 (VIB)
D9: U1.132 (PC21), U3.2 (VIA)
D13: R5.2, U1.68 (PB27)
D18: IWIFI.10, U1.4 (PA11)
D42: IWIFI.11, U1.71 (PA19)
D48: R42.1, R45.2, U1.97 (PC15)
D49: R43.1, R47.2, U1.96 (PC14)
D50: R48.1, R51.2, U1.95 (PC13)
D51: R49.1, R53.2, U1.94 (PC12)
D+: R3.1, U1.37 (DHSDP), X1.3, Z1.1
D-: R2.1, U1.38 (DHSDM), X1.2, Z2.1
DIN0: AMPSEAL1.32, R44.1
DIN1: AMPSEAL1.33, R46.1
DIN2: AMPSEAL1.34, R50.1
DIN3: AMPSEAL1.35, R52.1
DOUT0: AMPSEAL1.3, D7.C, T7.2 (D), T7.4 (D)
DOUT1: AMPSEAL1.4, D8.C, T8.2 (D), T8.4 (D)
DOUT2: AMPSEAL1.5, D5.C, T5.2 (D), T5.4 (D)
DOUT3: AMPSEAL1.6, D6.C, T6.2 (D), T6.4 (D)
DOUT4: AMPSEAL1.15, D3.C, T3.2 (D), T3.4 (D)
DOUT5: AMPSEAL1.16, D4.C, T4.2 (D), T4.4 (D)
DOUT6: AMPSEAL1.17, D1.C, T1.2 (D), T1.4 (D)
DOUT7: AMPSEAL1.18, D2.C, T2.2 (D), T2.4 (D)
ERASE_S: ERASE.P$1, U1.130 (PC0)
GND: +5V.C, +12V.C, AMPSEAL1.7, AMPSEAL1.8, AMPSEAL1.13, AMPSEAL1.14, AMPSEAL1.19, AMPSEAL1.29, AMPSEAL1.30, AMPSEAL1.31, C32.2, C33.2, C35.2, C36.2, C38.2, C39.2, C41.2, C42.2, C47.2, C48.2, C49.2, C50.2, C58.2, C59.2, C63.2, C64.2, C68.2, C69.2, C71.2, C72.2, C74.-, C75.2, C76.2, C78.1, C79.2, C80.2, D1.A, D2.A, D3.A, D4.A, D5.A, D6.A, D7.A, D8.A, IC3.3 (SHDN), IC3.4 (GND1), IC4.3 (SHDN), IC4.4 (GND1), IC7.3 (SHDN), IC7.4 (GND1), IC8.3 (SHDN), IC8.4 (GND1), IC9.10 (GND2), IC9.15 (GND2), IC9.16 (GND2), IC10.10 (GND2), IC10.15 (GND2), IC10.16 (GND2), IC11.4 (GND), OK1.2 (C), OK1.4 (C), OK2.2 (C), OK2.4 (C), R6.2, R7.2, R8.2, R9.2, R10.2, R11.2, R12.2, R13.2, R20.1, R22.1, R32.1, R34.1, T1.3 (S), T2.3 (S), T3.3 (S), T4.3 (S), T5.3 (S), T6.3 (S), T7.3 (S), T8.3 (S), TVS.A, U3.5 (GND2), U4.5 (GND2), U5.5 (GND2), U6.5 (GND2), U8.-VIN1, U8.-VIN2, ZEN.A
IGND: +3.3V.C, C1.2, C2.2, C3.2, C4.2, C5.2, C6.2, C7.2, C8.2, C9.2, C10.2, C11.2, C12.2, C13.2, C14.2, C15.2, C16.2, C17.2, C18.2, C19.2, C20.2, C21.2, C22.2, C23.2, C24.2, C25.2, C26.2, C27.2, C29.2, C30.2, C31.2, C34.2, C37.2, C40.2, C45.2, C46.2, C51.2, C52.2, C53.2, C54.2, C57.2, C60.2, C61.2, C62.2, C65.2, C66.2, C67.2, C70.2, C73.2, C77.2, C78.2, IC1.4 (V-), IC2.4 (V-), IC3.5 (GND2), IC4.5 (GND2), IC5.4 (V-), IC6.4 (V-), IC7.5 (GND2), IC8.5 (GND2), IC9.2 (GND1), IC9.7 (GND1), IC9.8 (GND1), IC10.2 (GND1), IC10.7 (GND1), IC10.8 (GND1), IWIFI.2, LED.C, OK1.5 (EMIT), OK1.7 (EMIT), OK2.5 (EMIT), OK2.7 (EMIT), R4.1, R24.2, R25.2, R36.2, R37.2, RESET.P$1, U1.12 (GND1), U1.33 (GNDPLL), U1.44 (GNDUTMI), U1.46 (JTAGSEL), U1.54 (GNDBU), U1.58 (GND2), U1.74 (GNDANA), U1.106 (GND3), U1.126 (GND4), U2.1 (ADJ), U3.4 (GND1), U4.4 (GND1), U5.4 (GND1), U6.4 (GND1), U7.PIN1 (NA1), U7.PIN2 (NA2), U7.PIN3 (E2), U7.PIN4 (VSS), U8.-VOUT, WIFI.C, X1.4, Y1.2 (GND), Y1.4 (GND), Z1.2, Z2.2
MASTER-RESET: C28.2, RESET.P$2, U1.47 (NRSTB)
MDRIVE0: R12.1, T7.1 (G), U6.6 (VOB)
MDRIVE1: R13.1, T8.1 (G), U6.7 (VOA)
MDRIVE2: R10.1, T5.1 (G), U5.6 (VOB)
MDRIVE3: R11.1, T6.1 (G), U5.7 (VOA)
MDRIVE4: R8.1, T3.1 (G), U4.6 (VOB)
MDRIVE5: R9.1, T4.1 (G), U4.7 (VOA)
MDRIVE6: R6.1, T1.1 (G), U3.6 (VOB)
MDRIVE7: R7.1, T2.1 (G), U3.7 (VOA)
unnamed: C47.1, IC3.2 (VIN), R16.1, R20.2
unnamed: +3.3V.A, R59.1
unnamed: D9.C, PTC.P$2 (2), TVS.C, ZEN.C
unnamed: +5V.A, R58.1
unnamed: LED.A, R5.1
unnamed: IC8.7 (VOUT+), R35.1
unnamed: IC8.6 (VOUT-), R31.1
unnamed: C56.2, IC6.2 (-IN), R27.1, R31.2
unnamed: IC3.7 (VOUT+), R21.1
unnamed: IC3.6 (VOUT-), R17.1
unnamed: C43.2, IC1.2 (-IN), R14.1, R17.2
unnamed: C53.1, IC1.3 (+IN), R21.2, R24.1
unnamed: C66.1, IC6.3 (+IN), R35.2, R37.1
unnamed: C63.1, IC8.2 (VIN), R30.1, R34.2
unnamed: IC4.7 (VOUT+), R23.1
unnamed: IC4.6 (VOUT-), R19.1
unnamed: C44.2, IC2.2 (-IN), R15.1, R19.2
unnamed: C54.1, IC2.3 (+IN), R23.2, R25.1
unnamed: C49.1, IC4.2 (VIN), R18.1, R22.2
unnamed: C69.1, R38.1, R39.1
unnamed: IC7.7 (VOUT+), R33.1
unnamed: R38.2, SJ1.2
unnamed: R39.2, SJ2.2
unnamed: R41.2, SJ4.2
unnamed: C72.1, R40.1, R41.1
unnamed: R40.2, SJ3.2
unnamed: OK1.1 (A), R44.2
unnamed: OK1.3 (A), R46.2
unnamed: OK1.8 (COL), R45.1
unnamed: OK1.6 (COL), R47.1
unnamed: IC7.6 (VOUT-), R29.1
unnamed: OK2.6 (COL), R53.1
unnamed: C55.2, IC5.2 (-IN), R26.1, R29.2
unnamed: OK2.8 (COL), R51.1
unnamed: C62.1, IC5.3 (+IN), R33.2, R36.1
unnamed: OK2.1 (A), R50.2
unnamed: C58.1, IC7.2 (VIN), R28.1, R32.2
unnamed: OK2.3 (A), R52.2
unnamed: +12V.A, R57.1
unnamed: IWIFI.12, R56.2
unnamed: R56.1, WIFI.A
unnamed: IWIFI.5, IWIFI.7
unnamed: R2.2, U1.43 (DFSDM)
unnamed: R3.2, U1.42 (DFSDP)
unnamed: R1.1, U1.53 (FWUP)
RX2: IWIFI.4, U1.5 (PA12)
RXD1: U7.PIN7 (WC)
SCL: R54.2, U1.87 (PB13), U7.PIN6 (SCL)
SDA: R55.2, U1.86 (PB12), U7.PIN5 (SDA)
TX2: IWIFI.3, U1.6 (PA13)
VBG: C27.1, R4.2, U1.40 (VBG)
VBUS: C29.1, U1.39 (VBUS), U2.3 (IN), X1.1
VDDANA: C10.1, C11.1, L1.2, U1.73 (VDDANA)
VDDOUT: C12.1, C13.1, C14.1, C15.1, C16.1, C17.1, C18.1, L4.1, U1.10 (VDDCORE1), U1.45 (VDDCORE2), U1.56 (VDDOUT), U1.61 (VDDCORE3), U1.104 (VDDCORE4), U1.124 (VDDCORE5)
VDDOUTMI: C8.1, C9.1, L2.2, U1.41 (VDDUTMI)
VDDPLL: C21.1, C22.1, L4.2, U1.34 (VDDPLL)
VIN(+12V): AMPSEAL1.1, D9.A
XIN: C24.1, U1.36 (XIN), Y1.1 (C1)
XIN32: C26.1, U1.48 (XIN32), Y2.P$2 (2)
XOUT: C23.1, U1.35 (XOUT), Y1.3 (C2)
XOUT32: C25.1, U1.49 (XOUT32), Y2.P$1 (1)

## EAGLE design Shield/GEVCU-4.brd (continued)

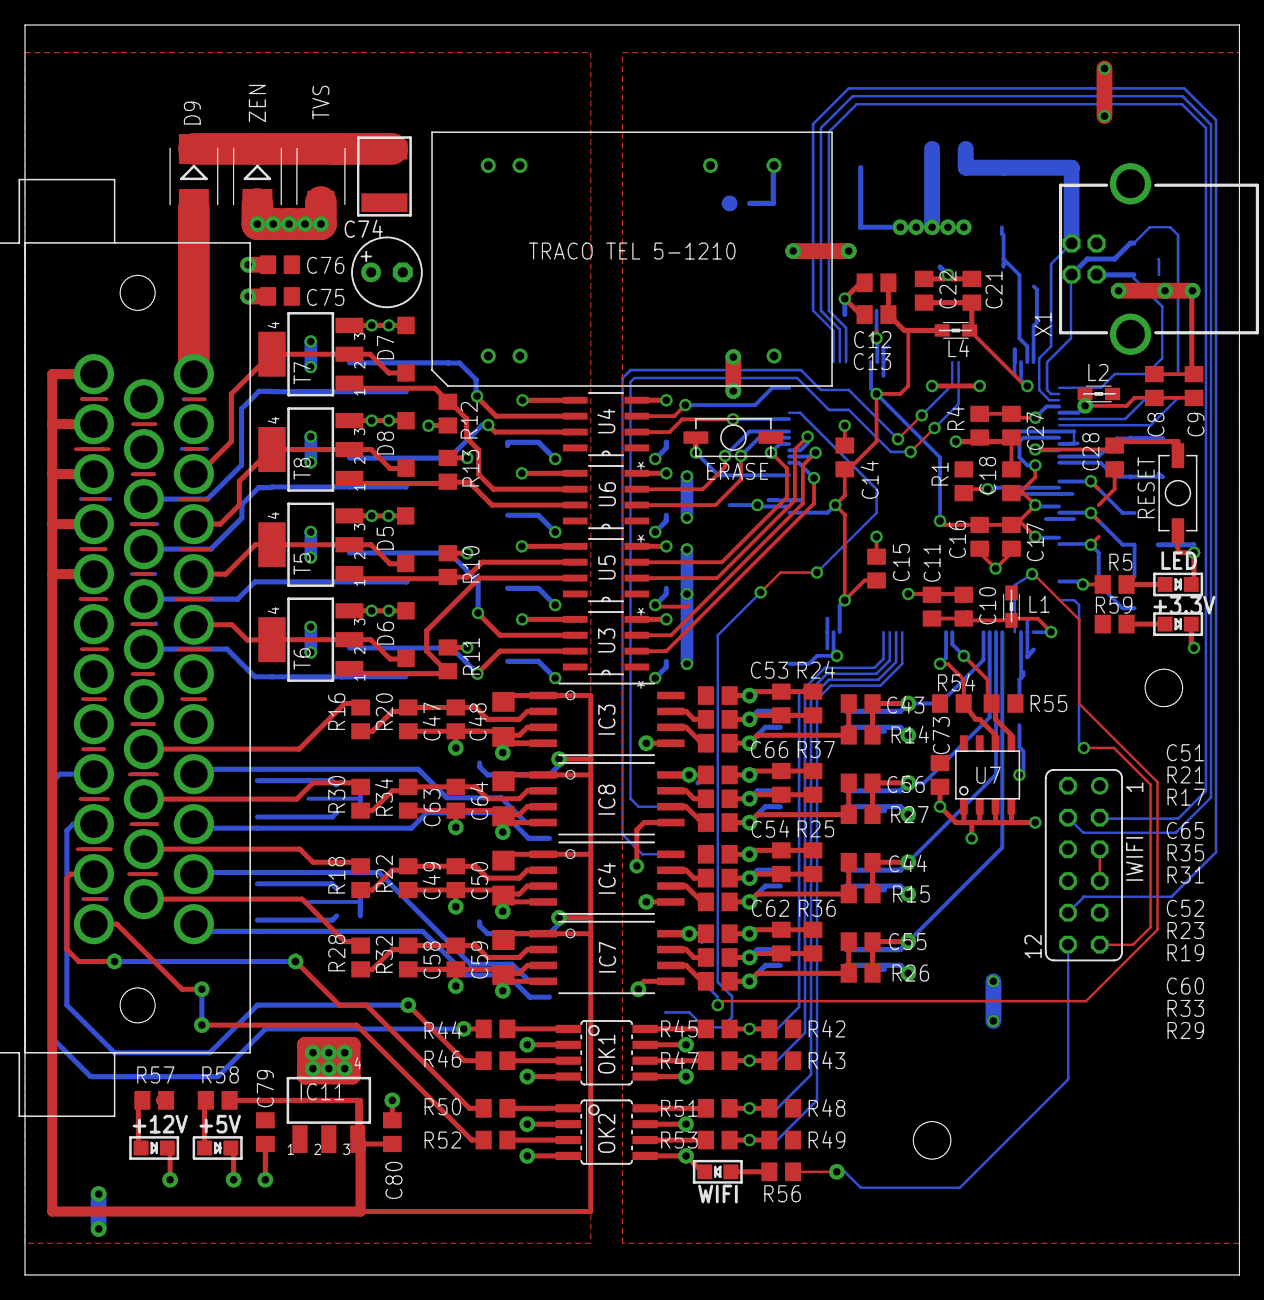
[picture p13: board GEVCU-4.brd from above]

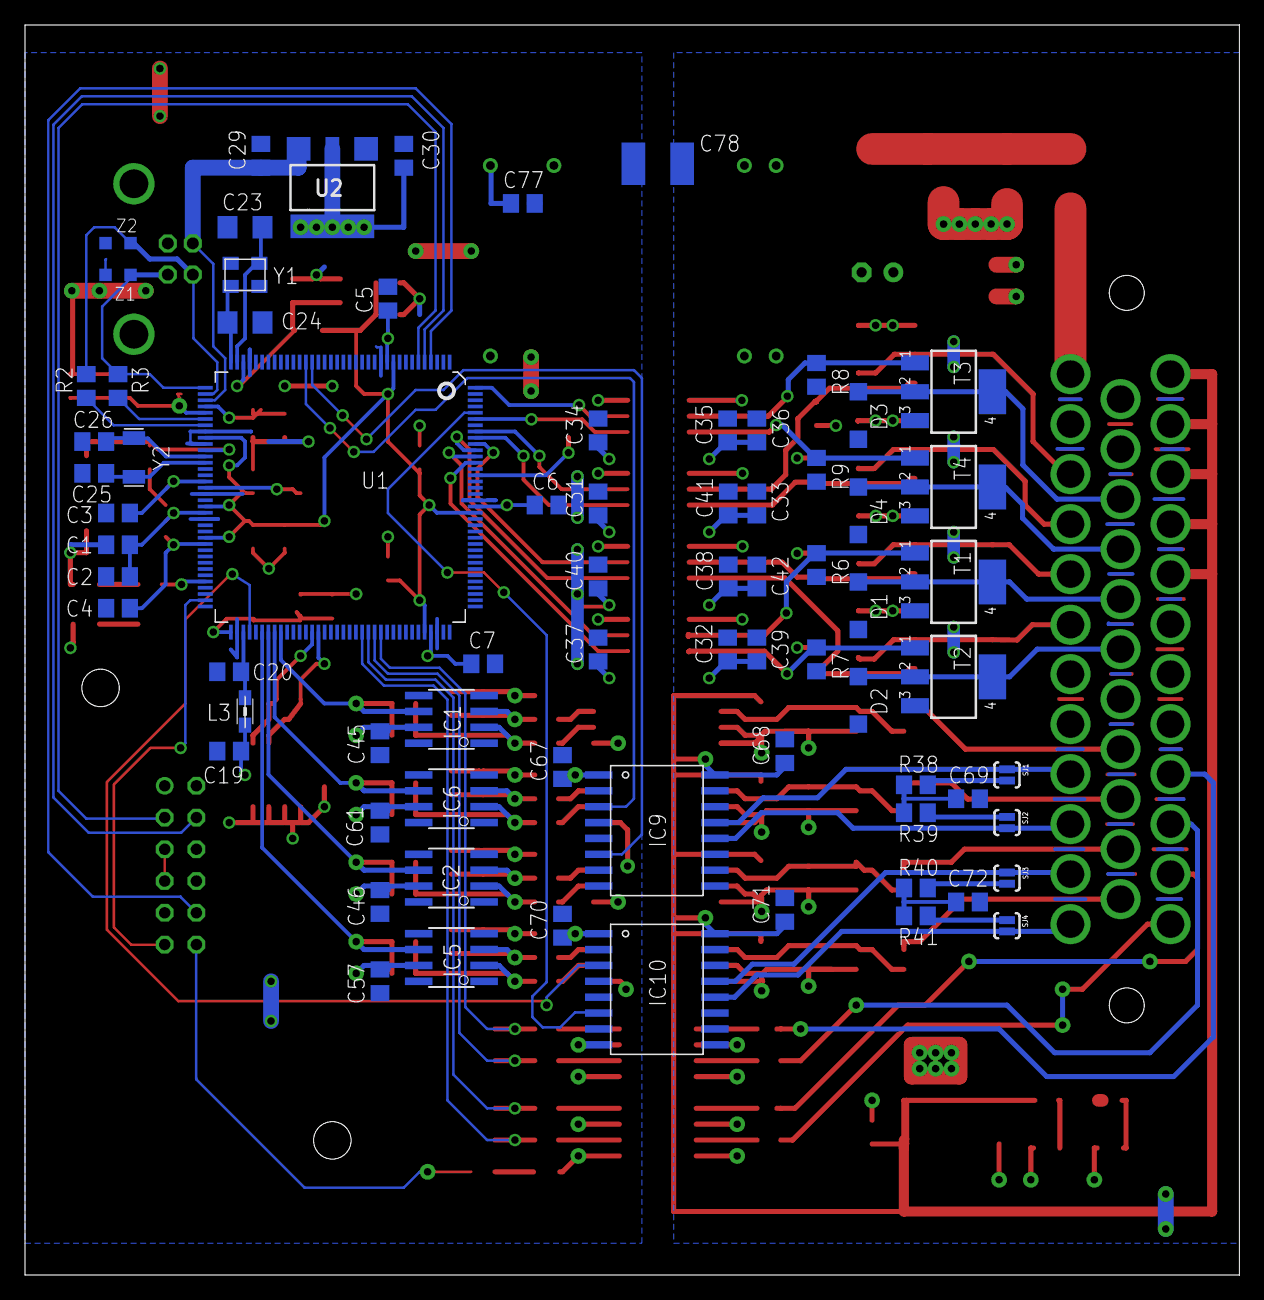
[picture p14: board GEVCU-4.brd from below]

Board: 2 copper layers, 97.2 x 100.0 mm, 202 parts (74 on the bottom side), 121 nets.

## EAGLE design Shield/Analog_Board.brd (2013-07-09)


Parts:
C1, C2, C5, C6, C7, C10, C11, C12, C14, C15, C16, C18: 0.1uf; C0603
C3, C4, C8, C9, C13, C17, C19, C20: 100pf; C0603
DC1: NMASIP8; NMA
IC1, IC4, IC6, IC8: INA105U; SO08
IC2, IC3, IC5, IC7: ACPL-C87A-000E; SO8-WIDE
JP1: M04LOCK; 1X04_LOCK
JP3, JP4, JP5, JP6, JP7: M08LOCK; 1X08_LOCK
JP8, JP9: M16LOCK; 1X16_LOCK
JP10: M06LOCK; 1X06_LOCK
R1, R7, R13, R19: 16k; R0603
R2, R8, R14, R20: 10k; R0603
R3, R4, R5, R6, R9, R10, R11, R12, R15, R16, R17, R18, R21, R22, R23, R24: 10k 1%; R0603

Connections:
3.3: JP10.2
5V: JP10.3
+5V: C2.1, C5.1, C7.1, C10.1, C12.1, C14.1, C16.1, C18.1, IC2.1 (VDD1), IC2.8 (VDD2), IC3.1 (VDD1), IC3.8 (VDD2), IC5.1 (VDD1), IC5.8 (VDD2), IC7.1 (VDD1), IC7.8 (VDD2)
+VOUT: DC1.5 (+VOUT), IC1.7 (V+), IC4.7 (V+), IC6.7 (V+), IC8.7 (V+)
-VOUT: DC1.7 (-VOUT), IC1.4 (V-), IC4.4 (V-), IC6.4 (V-), IC8.4 (V-)
A0: C4.2, IC1.6 (OUT), JP7.1, R5.2
A1: C9.2, IC4.6 (OUT), JP7.2, R11.2
A2: C19.2, IC6.6 (OUT), JP7.3, R17.2
A3: C20.2, IC8.6 (OUT), JP7.4, R23.2
A4: JP7.5
A5: JP7.6
A6: JP7.7
A7: JP7.8
A8: JP6.1
A9: JP6.2
A10: JP6.3
A11: JP6.4
A12: JP6.5
A13: JP6.6
A14: JP6.7
A15: JP6.8
AIN1: JP1.1, R1.2
AIN2: JP1.2, R7.2
AIN3: JP1.3, R13.2
AIN4: JP1.4, R19.2
AREF: JP3.8
D2: JP4.3
D3: JP4.4
D4: JP4.5
D5: JP4.6
D6: JP4.7
D7: JP4.8
D8: JP3.1
D9: JP3.2
D10: JP3.3
D11: JP3.4
D12: JP3.5
D13: JP3.6
D14: JP5.8
D15: JP5.7
D16: JP5.6
D17: JP5.5
D18: JP5.4
D19: JP5.3
D22: JP9.1
D23: JP8.16
D24: JP9.2
D25: JP8.15
D26: JP9.3
D27: JP8.14
D28: JP9.4
D29: JP8.13
D30: JP9.5
D31: JP8.12
D32: JP9.6
D33: JP8.11
D34: JP9.7
D35: JP8.10
D36: JP9.8
D37: JP8.9
D38: JP9.9
D39: JP8.8
D40: JP9.10
D41: JP8.7
D42: JP9.11
D43: JP8.6
D44: JP9.12
D45: JP8.5
D46: JP9.13
D47: JP8.4
D48: JP9.14
D49: JP8.3
D50: JP9.15
D51: JP8.2
D52: JP9.16
D53: JP8.1
GND: C1.2, C2.2, C3.1, C5.2, C6.2, C7.2, C8.1, C10.2, C11.2, C12.2, C13.1, C14.2, C15.2, C16.2, C17.1, C18.2, DC1.2 (-VIN), DC1.6 (COM), IC2.3 (SHDN), IC2.4 (GND1), IC2.5 (GND2), IC3.3 (SHDN), IC3.4 (GND1), IC3.5 (GND2), IC5.3 (SHDN), IC5.4 (GND1), IC5.5 (GND2), IC7.3 (SHDN), IC7.4 (GND1), IC7.5 (GND2), JP3.7, JP10.4, JP10.5, R2.1, R6.2, R8.1, R12.2, R14.1, R18.2, R20.1, R24.2
unnamed: C20.1, IC8.2 (-IN), R21.2, R23.1
unnamed: IC2.7 (VOUT+), R4.1
unnamed: IC2.6 (VOUT-), R3.1
unnamed: C4.1, IC1.2 (-IN), R3.2, R5.1
unnamed: C1.1, IC2.2 (VIN), R1.1, R2.2
unnamed: C3.2, IC1.3 (+IN), R4.2, R6.1
unnamed: C6.1, IC3.2 (VIN), R7.1, R8.2
unnamed: IC3.7 (VOUT+), R10.1
unnamed: IC3.6 (VOUT-), R9.1
unnamed: C9.1, IC4.2 (-IN), R9.2, R11.1
unnamed: C8.2, IC4.3 (+IN), R10.2, R12.1
unnamed: C11.1, IC5.2 (VIN), R13.1, R14.2
unnamed: IC5.7 (VOUT+), R16.1
unnamed: IC5.6 (VOUT-), R15.1
unnamed: C19.1, IC6.2 (-IN), R15.2, R17.1
unnamed: C13.2, IC6.3 (+IN), R16.2, R18.1
unnamed: C15.1, IC7.2 (VIN), R19.1, R20.2
unnamed: IC7.7 (VOUT+), R22.1
unnamed: IC7.6 (VOUT-), R21.1
unnamed: C17.2, IC8.3 (+IN), R22.2, R24.1
RES: JP10.1
RX0: JP4.1
SCL: JP5.1
SDA: JP5.2
TX1: JP4.2
VIN: DC1.1 (+VIN), JP10.6


Board: 2 copper layers, 101.6 x 53.3 mm, 62 parts (0 on the bottom side), 33 nets.

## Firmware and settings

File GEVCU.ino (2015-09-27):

/*
 GEVCU.ino
 
 Created: 1/4/2013 1:34:14 PM
 Author: Collin Kidder
 
 New, new plan: Allow for an arbitrary # of devices that can have both tick and canbus handlers. These devices register themselves
 into the handler framework and specify which sort of device they are. They can have custom tick intervals and custom can filters.
 The system automatically manages when to call the tick handlers and automatically filters canbus and sends frames to the devices.
 There is a facility to send data between devices by targetting a certain type of device. For instance, a motor controller
 can ask for any throttles and then retrieve the current throttle position from them.

Copyright (c) 2013 Collin Kidder, Michael Neuweiler, Charles Galpin

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
 */
 
/*Changelog removed. All changes are logged to GIT */

/*
Random comments on things that should be coded up soon:
4. It is a possibility that there should be support for actually controlling the power to some of the devices.
	For instance, power could be controlled to the +12V connection at the DMOC so that it can be power cycled
	in software. But, that uses up an input and people can just cycle the key (though that resets the GEVCU too)
5. Some people (like me, Collin) have a terrible habit of mixing several coding styles. It would be beneficial to
	continue to harmonize the source code - Perhaps use a tool to do this.
6. It should be possible to limit speed and/or torque in reverse so someone doesn't kill themselves or someone else
	while gunning it in reverse - The configuration variable is there and settable now. Just need to integrate it.
7. The DMOC code duplicates a bunch of functionality that the base class also used to implement. We've got to figure
	out where the overlaps are and fix it up so that as much as possible is done generically at the base MotorController
	class and not directly in the Dmoc class.
*/

#include "GEVCU.h"

// The following includes are required in the .ino file by the Arduino IDE in order to properly
// identify the required libraries for the build.
#include <due_rtc.h>
#include <due_can.h>
#include <due_wire.h>
#include <DueTimer.h>

//RTC_clock rtc_clock(XTAL); //init RTC with the external 32k crystal as a reference

//Evil, global variables
CanHandler *canHandlerEV;
CanHandler *canHandlerCar;
TickHandler *tickHandler;
PrefHandler *sysPrefs;
MemCache *memCache;
Heartbeat *heartbeat;
SerialConsole *serialConsole;
Device *wifiDevice;
Device *btDevice;


byte i = 0;


void sendWiReach(char* message)
{
  Serial2.println(message);
    delay(700);
    while (Serial2.available()) {SerialUSB.write(Serial2.read());}
}

void initWiReach()
{
SerialUSB.begin(115200); // use SerialUSB only as the programming port doesn't work
Serial2.begin(115200); // use Serial3 for GEVCU2, use Serial2 for GEVCU3+4

//sendWiReach("AT+iFD");//Host connection set to serial port
//delay(5000);
sendWiReach("AT+iHIF=1");//Host connection set to serial port
sendWiReach("AT+iBDRF=9");//Automatic baud rate on host serial port
sendWiReach("AT+iRPG=secret"); //Password for iChip wbsite
sendWiReach("AT+iWPWD=secret");//Password for our website
sendWiReach("AT+iWST0=0");//Connection security wap/wep/wap2 to no security
sendWiReach("AT+iWLCH=4");  //Wireless channel
sendWiReach("AT+iWLSI=GEVCU");//SSID
sendWiReach("AT+iWSEC=1");//IF security is used, set for WPA2-AES
sendWiReach("AT+iSTAP=1");//Act as AP
sendWiReach("AT+iDIP=192.168.3.10");//default ip - must be 10.x.x.x
sendWiReach("AT+iDPSZ=8");//DHCP pool size
sendWiReach("AT+iAWS=1");//Website on
sendWiReach("AT+iDOWN");//Powercycle reset
delay(5000);
SerialUSB.println("WiReach Wireless Module Initialized....");
}


  

//initializes all the system EEPROM values. Chances are this should be broken out a bit but
//there is only one checksum check for all of them so it's simple to do it all here.

void initSysEEPROM() {
	//three temporary storage places to make saving to EEPROM easy
	uint8_t eight;
	uint16_t sixteen;
	uint32_t thirtytwo;

	eight = 4; //GEVCU4 or GEVCU5 boards
	sysPrefs->write(EESYS_SYSTEM_TYPE, eight);

	sixteen = 1024; //no gain
	sysPrefs->write(EESYS_ADC0_GAIN, sixteen);
	sysPrefs->write(EESYS_ADC1_GAIN, sixteen);
	sysPrefs->write(EESYS_ADC2_GAIN, sixteen);
	sysPrefs->write(EESYS_ADC3_GAIN, sixteen);

	sixteen = 0; //no offset
	sysPrefs->write(EESYS_ADC0_OFFSET, sixteen);
	sysPrefs->write(EESYS_ADC1_OFFSET, sixteen);
	sysPrefs->write(EESYS_ADC2_OFFSET, sixteen);
	sysPrefs->write(EESYS_ADC3_OFFSET, sixteen);

	sixteen = 500; //multiplied by 1000 so 500k baud
	sysPrefs->write(EESYS_CAN0_BAUD, sixteen);
	sysPrefs->write(EESYS_CAN1_BAUD, sixteen);

	sixteen = 11520; //multiplied by 10
	sysPrefs->write(EESYS_SERUSB_BAUD, sixteen);

	sixteen = 100; //multiplied by 1000
	sysPrefs->write(EESYS_TWI_BAUD, sixteen);

	sixteen = 100; //number of ticks per second
	sysPrefs->write(EESYS_TICK_RATE, sixteen);

	thirtytwo = 0;
	sysPrefs->write(EESYS_RTC_TIME, thirtytwo);
	sysPrefs->write(EESYS_RTC_DATE, thirtytwo);

	eight = 5; //how many RX mailboxes
	sysPrefs->write(EESYS_CAN_RX_COUNT, eight);

	thirtytwo = 0x7f0; //standard frame, ignore bottom 4 bits
	sysPrefs->write(EESYS_CAN_MASK0, thirtytwo);
	sysPrefs->write(EESYS_CAN_MASK1, thirtytwo);
	sysPrefs->write(EESYS_CAN_MASK2, thirtytwo);
	sysPrefs->write(EESYS_CAN_MASK3, thirtytwo);
	sysPrefs->write(EESYS_CAN_MASK4, thirtytwo);

	thirtytwo = 0x230;
	sysPrefs->write(EESYS_CAN_FILTER0, thirtytwo);
	sysPrefs->write(EESYS_CAN_FILTER1, thirtytwo);
	sysPrefs->write(EESYS_CAN_FILTER2, thirtytwo);

	thirtytwo = 0x650;
	sysPrefs->write(EESYS_CAN_FILTER3, thirtytwo);
	sysPrefs->write(EESYS_CAN_FILTER4, thirtytwo);

	thirtytwo = 0; //ok, not technically 32 bytes but the four zeros still shows it is unused.
	sysPrefs->write(EESYS_WIFI0_SSID, thirtytwo);
	sysPrefs->write(EESYS_WIFI1_SSID, thirtytwo);
	sysPrefs->write(EESYS_WIFI2_SSID, thirtytwo);
	sysPrefs->write(EESYS_WIFIX_SSID, thirtytwo);

	eight = 0; //no channel, DHCP off, B mode
	sysPrefs->write(EESYS_WIFI0_CHAN, eight);
	sysPrefs->write(EESYS_WIFI0_DHCP, eight);
	sysPrefs->write(EESYS_WIFI0_MODE, eight);

	sysPrefs->write(EESYS_WIFI1_CHAN, eight);
	sysPrefs->write(EESYS_WIFI1_DHCP, eight);
	sysPrefs->write(EESYS_WIFI1_MODE, eight);

	sysPrefs->write(EESYS_WIFI2_CHAN, eight);
	sysPrefs->write(EESYS_WIFI2_DHCP, eight);
	sysPrefs->write(EESYS_WIFI2_MODE, eight);

	sysPrefs->write(EESYS_WIFIX_CHAN, eight);
	sysPrefs->write(EESYS_WIFIX_DHCP, eight);
	sysPrefs->write(EESYS_WIFIX_MODE, eight);

	thirtytwo = 0;
	sysPrefs->write(EESYS_WIFI0_IPADDR, thirtytwo);
	sysPrefs->write(EESYS_WIFI1_IPADDR, thirtytwo);
	sysPrefs->write(EESYS_WIFI2_IPADDR, thirtytwo);
	sysPrefs->write(EESYS_WIFIX_IPADDR, thirtytwo);

	sysPrefs->write(EESYS_WIFI0_KEY, thirtytwo);
	sysPrefs->write(EESYS_WIFI1_KEY, thirtytwo);
	sysPrefs->write(EESYS_WIFI2_KEY, thirtytwo);
	sysPrefs->write(EESYS_WIFIX_KEY, thirtytwo);

	eight = 1;
	sysPrefs->write(EESYS_LOG_LEVEL, eight);

	sysPrefs->saveChecksum();
}

void createObjects() {
	PotThrottle *paccelerator = new PotThrottle();
	CanThrottle *caccelerator = new CanThrottle();
	PotBrake *pbrake = new PotBrake();
	CanBrake *cbrake = new CanBrake();
	DmocMotorController *dmotorController = new DmocMotorController();
    CodaMotorController *cmotorController = new CodaMotorController();
        DCDCController *dcdcController = new DCDCController();
	BrusaMotorController *bmotorController = new BrusaMotorController();
	ThinkBatteryManager *BMS = new ThinkBatteryManager();
	ELM327Emu *emu = new ELM327Emu();
	ICHIPWIFI *iChip = new ICHIPWIFI();	
        EVIC *eVIC = new EVIC();
}
     void initializeDevices() {
	DeviceManager *deviceManager = DeviceManager::getInstance();

	//heartbeat is always enabled now
	heartbeat = new Heartbeat();
	Logger::info("add: Heartbeat (id: %X, %X)", HEARTBEAT, heartbeat);
	heartbeat->setup();

	//fault handler is always enabled too - its also statically allocated so no using -> here
	//This is initialized before the other devices so that they can go ahead and use it if they fault upon start up
	faultHandler.setup();

	/*
	We used to instantiate all the objects here along with other code. To simplify things this is done somewhat
	automatically now. Just instantiate your new device object in createObjects above. This takes care of the details
	so long as you follow the template of how other devices were coded.
	*/
	createObjects(); 

	/*
	 *	We defer setting up the devices until here. This allows all objects to be instantiated
	 *	before any of them set up. That in turn allows the devices to inspect what else is
	 *	out there as they initialize. For instance, a motor controller could see if a BMS
	 *	exists and supports a function that the motor controller wants to access.
	 */
	deviceManager->sendMessage(DEVICE_ANY, INVALID, MSG_STARTUP, NULL);

}

void setup() {
	sys_boot_setup(); //sets digital outputs to "off" right as soon as the sketch gets control.
	
        //delay(5000);  //This delay lets you see startup.  But it breaks DMOC645 really badly.  You have to have comm way before 5 seconds.
       
        //initWiReach();
	pinMode(BLINK_LED, OUTPUT);
	digitalWrite(BLINK_LED, LOW);
        SerialUSB.begin(CFG_SERIAL_SPEED);
	SerialUSB.println(CFG_VERSION);
	SerialUSB.print("Build number: ");
	SerialUSB.println(CFG_BUILD_NUM);
	Wire.begin();
	Logger::info("TWI init ok");
	memCache = new MemCache();
	Logger::info("add MemCache (id: %X, %X)", MEMCACHE, memCache);
	memCache->setup();
	sysPrefs = new PrefHandler(SYSTEM);
	if (!sysPrefs->checksumValid()) 
            {
	      Logger::info("Initializing EEPROM");
	      initSysEEPROM();
             // initWiReach();
	    } 
          else {Logger::info("Using existing EEPROM values");}//checksum is good, read in the values stored in EEPROM

	uint8_t loglevel;
	sysPrefs->read(EESYS_LOG_LEVEL, &loglevel);
	Logger::setLoglevel((Logger::LogLevel)loglevel);
	Logger::setLoglevel((Logger::LogLevel)1);
	sys_early_setup();     
	tickHandler = TickHandler::getInstance();
	canHandlerEV = CanHandler::getInstanceEV();
	canHandlerCar = CanHandler::getInstanceCar();
	canHandlerEV->initialize();
	canHandlerCar->initialize();
	setup_sys_io(); //get calibration data for system IO
	Logger::info("SYSIO init ok");

	initializeDevices();
    serialConsole = new SerialConsole(memCache, heartbeat);
	serialConsole->printMenu();
	wifiDevice = DeviceManager::getInstance()->getDeviceByID(ICHIP2128);
	btDevice = DeviceManager::getInstance()->getDeviceByID(ELM327EMU);
    DeviceManager::getInstance()->sendMessage(DEVICE_WIFI, ICHIP2128, MSG_CONFIG_CHANGE, NULL); //Load configuration variables into WiFi Web Configuration screen
	Logger::info("System Ready");
}

void loop() {

#ifdef CFG_TIMER_USE_QUEUING
	tickHandler->process();
#endif

	// check if incoming frames are available in the can buffer and process them
	canHandlerEV->process();
	canHandlerCar->process();

	serialConsole->loop();
	//TODO: this is dumb... shouldn't have to manually do this. Devices should be able to register loop functions
	if ( wifiDevice != NULL ) {
		((ICHIPWIFI*)wifiDevice)->loop();
	}

	//if (btDevice != NULL) {
	//	((ELM327Emu*)btDevice)->loop();
	//}

	//this should still be here. It checks for a flag set during an interrupt
	sys_io_adc_poll();
}

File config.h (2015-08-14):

/*
 * config.h
 *
 * Defines the components to be used in the GEVCU and allows the user to configure
 * static parameters.
 *
 * Note: Make sure with all pin defintions of your hardware that each pin number is
 *       only defined once.

 Copyright (c) 2013 Collin Kidder, Michael Neuweiler, Charles Galpin

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
THE SOFTWARE IS PROVIDED "AS IS", WITHOUT WARRANTY OF ANY KIND,
EXPRESS OR IMPLIED, INCLUDING BUT NOT LIMITED TO THE WARRANTIES OF
MERCHANTABILITY, FITNESS FOR A PARTICULAR PURPOSE AND NONINFRINGEMENT.
IN NO EVENT SHALL THE AUTHORS OR COPYRIGHT HOLDERS BE LIABLE FOR ANY
CLAIM, DAMAGES OR OTHER LIABILITY, WHETHER IN AN ACTION OF CONTRACT,
TORT OR OTHERWISE, ARISING FROM, OUT OF OR IN CONNECTION WITH THE
SOFTWARE OR THE USE OR OTHER DEALINGS IN THE SOFTWARE.
 *      Author: Michael Neuweiler
 */

#ifndef CONFIG_H_
#define CONFIG_H_

#include <due_can.h>

#define CFG_BUILD_NUM	5220        //increment this every time a git commit is done. 
#define CFG_VERSION "GEVCU 2015-02-19"


/*
 * SERIAL CONFIGURATION
 */
#define CFG_SERIAL_SPEED 115200
//#define SerialUSB Serial // re-route serial-usb output to programming port ;) comment if output should go to std usb


//The defines that used to be here to configure devices are gone now.
//The EEPROM stores which devices to bring up at start up and all
//devices are programmed into the firware at the same time.

/*
 * TIMER INTERVALS
 *
 * specify the intervals (microseconds) at which each device type should be "ticked"
 * try to use the same numbers for several devices because then they will share
 * the same timer (out of a limited number of 9 timers).
 */
#define CFG_TICK_INTERVAL_HEARTBEAT			2000000
#define CFG_TICK_INTERVAL_POT_THROTTLE		        40000
#define CFG_TICK_INTERVAL_CAN_THROTTLE			40000
#define CFG_TICK_INTERVAL_MOTOR_CONTROLLER		40000
#define CFG_TICK_INTERVAL_MOTOR_CONTROLLER_DMOC		40000
#define CFG_TICK_INTERVAL_MOTOR_CONTROLLER_CODAUQM	10000
#define CFG_TICK_INTERVAL_MOTOR_CONTROLLER_BRUSA	20000
#define CFG_TICK_INTERVAL_MEM_CACHE			40000
#define CFG_TICK_INTERVAL_BMS_THINK			500000
#define CFG_TICK_INTERVAL_WIFI				200000
#define CFG_TICK_INTERVAL_DCDC                          200000
#define CFG_TICK_INTERVAL_EVIC                          100000


/*
 * CAN BUS CONFIGURATION
 */
#define CFG_CAN0_SPEED CAN_BPS_500K // specify the speed of the CAN0 bus (EV)
#define CFG_CAN1_SPEED CAN_BPS_250K // specify the speed of the CAN1 bus (Car)
#define CFG_CAN0_NUM_RX_MAILBOXES 9 // amount of CAN bus receive mailboxes for CAN0
#define CFG_CAN1_NUM_RX_MAILBOXES 9 // amount of CAN bus receive mailboxes for CAN1
#define CFG_CANTHROTTLE_MAX_NUM_LOST_MSG 3 // maximum number of lost messages allowed

/*
 * MISCELLANEOUS
 *
 */
#define CFG_THROTTLE_TOLERANCE  150 //the max that things can go over or under the min/max without fault - 1/10% each #


/*
 * HARD CODED PARAMETERS
 *
 * If USE_HARD_CODED is defined or the checksum of the parameters stored in EEPROM,
 * the parameter values defined here are used instead of those stored in the EEPROM.
 */
//#define USE_HARD_CODED
#define ThrottleNumPots			1		//# of pots to use by default
#define ThrottleADC1			0		//Which pin to use
#define ThrottleADC2			1		//Which pin to use
#define ThrottleSubtype			1		//subtype 1 is a standard linear pot throttle
#define ThrottleRegenMinValue	270		//where does Regen stop (1/10 of percent)
#define ThrottleRegenMaxValue	30		//where Regen is at maximum (1/10 of percent)
#define ThrottleFwdValue		300		//where does forward motion start
#define ThrottleMapValue		750		//Where is the 1/2 way point for throttle
#define ThrottleMinRegenValue	0		//how many percent of full power to use at minimal regen
#define ThrottleMaxRegenValue	50		//how many percent of full power to use at maximum regen
#define ThrottleCreepValue		0		//how many percent of full power to use at creep
#define ThrottleMaxErrValue		150		//tenths of percentage allowable deviation between pedals
#define Throttle1MinValue		95		//Value ADC reads when pedal is up
#define Throttle1MaxValue		3150		//Value ADC reads when pedal fully depressed
#define Throttle2MinValue		0		//Value ADC reads when pedal is up
#define Throttle2MaxValue		0	//Value ADC reads when pedal fully depressed
#define BrakeMinValue			100		//Value ADC reads when brake is not pressed
#define BrakeMaxValue			3200		//Value ADC reads when brake is pushed all of the way down
#define BrakeMinRegenValue		0		//percent of full power to use for brake regen (min)
#define BrakeMaxRegenValue		50		//percent of full power to use for brake regen (max)
#define BrakeADC				2       //which ADC pin to use
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

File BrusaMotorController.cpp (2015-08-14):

/*
 * BrusaMotorController.cpp
 *
 *
 Copyright (c) 2013 Collin Kidder, Michael Neuweiler, Charles Galpin

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
 */

#include "BrusaMotorController.h"

/*
 Warning:
 At high speed disable the DMC_EnableRq can be dangerous because a field weakening current is
 needed to achieve zero torque. Switching off the DMC in such a situation will make heavy regenerat-
 ing torque that can't be controlled.
 */

/*
 * Constructor
 */
BrusaMotorController::BrusaMotorController() : MotorController() {
	prefsHandler = new PrefHandler(BRUSA_DMC5);
	torqueAvailable = 0;
	maxPositiveTorque = 0;
	minNegativeTorque = 0;
	limiterStateNumber = 0;

	tickCounter = 0;

	commonName = "Brusa DMC5 Inverter";
}

/*
 * Setup the device if it is enabled in configuration.
 */
void BrusaMotorController::setup() {
	TickHandler::getInstance()->detach(this);

	Logger::info("add device: Brusa DMC5 (id: %X, %X)", BRUSA_DMC5, this);

	loadConfiguration();
	MotorController::setup(); // run the parent class version of this function

	// register ourselves as observer of 0x258-0x268 and 0x458 can frames
	CanHandler::getInstanceEV()->attach(this, CAN_MASKED_ID_1, CAN_MASK_1, false);
	CanHandler::getInstanceEV()->attach(this, CAN_MASKED_ID_2, CAN_MASK_2, false);

	TickHandler::getInstance()->attach(this, CFG_TICK_INTERVAL_MOTOR_CONTROLLER_BRUSA);
}

/*
 * Process event from the tick handler.
 *
 * The super-class requests desired levels from the throttle and
 * brake and decides which one to apply.
 */
void BrusaMotorController::handleTick() {
	MotorController::handleTick(); // call parent
	tickCounter++;

	sendControl();	// send CTRL every 20ms
	if (tickCounter > 4) {
		sendControl2();	// send CTRL_2 every 100ms
		sendLimits();	// send LIMIT every 100ms
		tickCounter = 0;
	}
}

/*
 * Send DMC_CTRL message to the motor controller.
 *
 * This message controls the power-stage in the controller, clears the error latch
 * in case errors were detected and requests the desired torque / speed.
 */
void BrusaMotorController::sendControl() {
	BrusaMotorControllerConfiguration *config = (BrusaMotorControllerConfiguration *)getConfiguration();
	prepareOutputFrame(CAN_ID_CONTROL);

	speedRequested = 0;
	torqueRequested = 0;

	outputFrame.data.bytes[0] = enablePositiveTorqueSpeed; // | enableNegativeTorqueSpeed;
	if (faulted) {
		outputFrame.data.bytes[0] |= clearErrorLatch;
	} else {
		if ((running || speedActual > 1000) && !getDigital(1)) { // see warning about field weakening current to prevent uncontrollable regen
			outputFrame.data.bytes[0] |= enablePowerStage;
		}
		if (running) {
			if (config->enableOscillationLimiter)
				outputFrame.data.bytes[0] |= enableOscillationLimiter;

			if (powerMode == modeSpeed) {
				outputFrame.data.bytes[0] |= enableSpeedMode;
				speedRequested = throttleRequested * config->speedMax / 1000;
				torqueRequested = config->torqueMax; // positive number used for both speed directions
			} else { // torque mode
				speedRequested = config->speedMax; // positive number used for both torque directions
				torqueRequested = throttleRequested * config->torqueMax / 1000;
			}

			// set the speed in rpm
			outputFrame.data.bytes[2] = (speedRequested & 0xFF00) >> 8;
			outputFrame.data.bytes[3] = (speedRequested & 0x00FF);

			// set the torque in 0.01Nm (GEVCU uses 0.1Nm -> multiply by 10)
			outputFrame.data.bytes[4] = ((torqueRequested * 10) & 0xFF00) >> 8;
			outputFrame.data.bytes[5] = ((torqueRequested * 10) & 0x00FF);
		}
	}

	if (Logger::isDebug())
		Logger::debug(BRUSA_DMC5, "requested Speed: %l rpm, requested Torque: %f Nm", speedRequested, (float)torqueRequested/10.0F);

	CanHandler::getInstanceEV()->sendFrame(outputFrame);
}

/*
 * Send DMC_CTRL2 message to the motor controller.
 *
 * This message controls the mechanical power limits for motor- and regen-mode.
 */
void BrusaMotorController::sendControl2() {
	BrusaMotorControllerConfiguration *config = (BrusaMotorControllerConfiguration *)getConfiguration();

	prepareOutputFrame(CAN_ID_CONTROL_2);
	outputFrame.data.bytes[0] = ((config->torqueSlewRate * 10) & 0xFF00) >> 8;
	outputFrame.data.bytes[1] = ((config->torqueSlewRate * 10) & 0x00FF);
	outputFrame.data.bytes[2] = (config->speedSlewRate & 0xFF00) >> 8;
	outputFrame.data.bytes[3] = (config->speedSlewRate & 0x00FF);
	outputFrame.data.bytes[4] = (config->maxMechanicalPowerMotor & 0xFF00) >> 8;
	outputFrame.data.bytes[5] = (config->maxMechanicalPowerMotor & 0x00FF);
	outputFrame.data.bytes[6] = (config->maxMechanicalPowerRegen & 0xFF00) >> 8;
	outputFrame.data.bytes[7] = (config->maxMechanicalPowerRegen & 0x00FF);

	CanHandler::getInstanceEV()->sendFrame(outputFrame);
}

/*
 * Send DMC_LIM message to the motor controller.
 *
 * This message controls the electrical limits in the controller.
 */
void BrusaMotorController::sendLimits() {
	BrusaMotorControllerConfiguration *config = (BrusaMotorControllerConfiguration *)getConfiguration();

	prepareOutputFrame(CAN_ID_LIMIT);
	outputFrame.data.bytes[0] = (config->dcVoltLimitMotor & 0xFF00) >> 8;
	outputFrame.data.bytes[1] = (config->dcVoltLimitMotor & 0x00FF);
	outputFrame.data.bytes[2] = (config->dcVoltLimitRegen & 0xFF00) >> 8;
	outputFrame.data.bytes[3] = (config->dcVoltLimitRegen & 0x00FF);
	outputFrame.data.bytes[4] = (config->dcCurrentLimitMotor & 0xFF00) >> 8;
	outputFrame.data.bytes[5] = (config->dcCurrentLimitMotor & 0x00FF);
	outputFrame.data.bytes[6] = (config->dcCurrentLimitRegen & 0xFF00) >> 8;
	outputFrame.data.bytes[7] = (config->dcCurrentLimitRegen & 0x00FF);

	CanHandler::getInstanceEV()->sendFrame(outputFrame);
}

/*
 * Prepare the CAN transmit frame.
 * Re-sets all parameters in the re-used frame.
 */
void BrusaMotorController::prepareOutputFrame(uint32_t id) {
	outputFrame.length = 8;
	outputFrame.id = id;
	outputFrame.extended = 0;
	outputFrame.rtr = 0;

	outputFrame.data.bytes[1] = 0;
	outputFrame.data.bytes[2] = 0;
	outputFrame.data.bytes[3] = 0;
	outputFrame.data.bytes[4] = 0;
	outputFrame.data.bytes[5] = 0;
	outputFrame.data.bytes[6] = 0;
	outputFrame.data.bytes[7] = 0;
}

/*
 * Processes an event from the CanHandler.
 *
 * In case a CAN message was received which pass the masking and id filtering,
 * this method is called. Depending on the ID of the CAN message, the data of
 * the incoming message is processed.
 */
void BrusaMotorController::handleCanFrame( CAN_FRAME *frame) {
	switch (frame->id) {
	case CAN_ID_STATUS:
		processStatus(frame->data.bytes);
		break;
	case CAN_ID_ACTUAL_VALUES:
		processActualValues(frame->data.bytes);
		break;
	case CAN_ID_ERRORS:
		processErrors(frame->data.bytes);
		break;
	case CAN_ID_TORQUE_LIMIT:
		processTorqueLimit(frame->data.bytes);
		break;
	case CAN_ID_TEMP:
		processTemperature(frame->data.bytes);
		break;
	default:
		Logger::warn(BRUSA_DMC5, "received unknown frame id %X", frame->id);
	}
}
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

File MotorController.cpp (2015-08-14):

/*
 * MotorController.cpp
 *
 * Parent class for all motor controllers.
 *
Copyright (c) 2013 Collin Kidder, Michael Neuweiler, Charles Galpin

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
 */ 
 
#include "MotorController.h"
 
MotorController::MotorController() : Device() {
	ready = false;
	running = false;
	faulted = false;
	warning = false;

	temperatureMotor = 0;
	temperatureInverter = 0;
	temperatureSystem = 0;

	statusBitfield1 = 0;
	statusBitfield2 = 0;
	statusBitfield3 = 0;
	statusBitfield4 = 0;

	powerMode = modeTorque;
	throttleRequested = 0;
	speedRequested = 0;
	speedActual = 0;
	torqueRequested = 0;
	torqueActual = 10;
	torqueAvailable = 0;
	mechanicalPower = 0;

	selectedGear = NEUTRAL;
        operationState=ENABLE;

	dcVoltage = 0;
	dcCurrent = 0;
	acCurrent = 0;
	kiloWattHours = 0;
	nominalVolts = 0;

	donePrecharge = false;  
        prelay = false;
        coolflag = false;
        skipcounter=0;
        testenableinput=0;
        testreverseinput=0;
        premillis=0;



}

void MotorController::setup() {
  
	MotorControllerConfiguration *config = (MotorControllerConfiguration *)getConfiguration();
	statusBitfield1 = 0;
	statusBitfield2 = 0;
	statusBitfield3 = 0;
	statusBitfield4 = 0;
        prefsHandler->read(EEMC_KILOWATTHRS, &kiloWattHours); //retrieve kilowatt hours from EEPROM
        nominalVolts=config->nominalVolt;
        capacity=config->capacity;
        donePrecharge=false;
        premillis=millis();      

    if(config->prechargeR==12345)
      {  
	torqueActual=2;
        dcCurrent=1501;
        dcVoltage=3320;
        
      }
    Logger::console("PRELAY=%i - Current PreCharge Relay output", config->prechargeRelay);
    Logger::console("MRELAY=%i - Current Main Contactor Relay output", config->mainContactorRelay);
    Logger::console("PREDELAY=%i - Precharge delay time", config->prechargeR);
	 
    //show our work
    Logger::console("PRECHARGING...DOUT0:%d, DOUT1:%d, DOUT2:%d, DOUT3:%d,DOUT4:%d, DOUT5:%d, DOUT6:%d, DOUT7:%d", getOutput(0), getOutput(1), getOutput(2), getOutput(3),getOutput(4), getOutput(5), getOutput(6), getOutput(7));
    coolflag=false;
    
    Device::setup();
   
}


void MotorController::handleTick() {

      MotorControllerConfiguration *config = (MotorControllerConfiguration *)getConfiguration();
     
    //Set status annunciators
     if(ready) statusBitfield1 |=1 << 15;else statusBitfield1 &= ~(1 <<15);
     if(running) statusBitfield1 |=1 << 14;else statusBitfield1 &= ~(1 <<14);
     if(warning) statusBitfield1 |=1 << 10;else statusBitfield1 &= ~(1 <<10);
     if(faulted) statusBitfield1 |=1 << 9;else statusBitfield1 &= ~(1 <<9);
     
     //Calculate killowatts and kilowatt hours 
       mechanicalPower=dcVoltage*dcCurrent/10000; //In kilowatts. DC voltage is x10
       if (dcVoltage>nominalVolts && torqueActual>0) {kiloWattHours=1;} //If our voltage is higher than fully charged with no regen, zero our kwh meter
       if (milliStamp>millis()) {milliStamp=0;} //In case millis rolls over to zero while running
       kiloWattHours+=(millis()-milliStamp)*mechanicalPower;//We assume here that power is at current level since last tick and accrue in kilowattmilliseconds.
       milliStamp=millis();              //reset our kwms timer for next check
       
       
     //Throttle check
	Throttle *accelerator = DeviceManager::getInstance()->getAccelerator();
	Throttle *brake = DeviceManager::getInstance()->getBrake();
	if (accelerator)
		throttleRequested = accelerator->getLevel();
	if (brake && brake->getLevel() < -10 && brake->getLevel() < accelerator->getLevel()) //if the brake has been pressed it overrides the accelerator.
		throttleRequested = brake->getLevel();
	//Logger::debug("Throttle: %d", throttleRequested);


      if (!donePrecharge)checkPrecharge();
          

	if(skipcounter++ > 30)    //A very low priority loop for checks that only need to be done once per second.
	{  
            skipcounter=0; //Reset our laptimer
              
                
                //Some test simulations if precharge time is set to 12345
		if(config->prechargeR==12345)
                  {
		    dcVoltage--;  
	            if (torqueActual < -500)
                      {
                        torqueActual=20;
                      }
                     else 
                       {
                         torqueActual=-650;
                       }
                        if (dcCurrent < 0)
                      {
                        dcCurrent=120;
                      }
                     else 
                       {
                         dcCurrent=-65;
                       }
                    if (temperatureInverter < config->coolOn*10)
                      {
                        temperatureInverter=(config->coolOn+2)*10;
                      }
                      else 
                        {
                          temperatureInverter=(config->coolOff-2)*10;
                        }
                
                    if (throttleRequested < 500)
                      {
                        throttleRequested=500;
                      }
                      else 
                      {
                        throttleRequested=0;
                      }
                    if(testenableinput)
                      {
                        testenableinput=false;
                      }
                      else 
                        {
                          testenableinput=true;
                        }
                        
                    if(testreverseinput)
                      {
                        testreverseinput=false;
                      }
                      else 
                        {
                          testreverseinput=true;
                        }
		  }	
            coolingcheck();
            checkBrakeLight();
            checkEnableInput();
            checkReverseInput();
            checkReverseLight();
          
            //Store kilowatt hours, but only once in awhile.
            prefsHandler->write(EEMC_KILOWATTHRS, kiloWattHours);
	    prefsHandler->saveChecksum();

   	}
}
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

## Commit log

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2013-01-15 A start to actually implementing the firmware. It doesn't work yet though.
    [ThrottleFiltering.xlsx]
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2013-01-16 Fixed up a variety of mental deficiencies on my part in the code for throttle calculation. It seems to work now.
    [pedal_pot.cpp]
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2013-02-01 Tested working with Code Blocks Arduino edition version 1/31/2013
    Fixed up throttle code, made it verify my accelerator pedal output. This would be a setup where there are two pedal pots, one is to be twice the value of the other. If your pedal doesn't match then adjust accordingly. Also, regen is disabled.
    Added a mode to the menu where the accelerator can be used to drive the motor instead of merely doing an RPM ramp.
    [pedal_pot.cpp]
2013-02-03 Renamed some things
    Moved ENUMs into the classes they belong with to better scope them
    Changed the parameters of functions to enums where appropriate to enforce proper values
    Added status reporting for pot based throttle so that it reports what caused an error
    Pretty much totally reworked how the throttle code works so that it properly handles throttles which go either way (high to low or low to high). Now pretty much any pot based throttle should be able to be used. Initial caution would, however, be advisable when testing a new pedal.
    Updated the readme to explain how to get started with the project.
    [dmoc.cpp, pedal_pot.cpp]
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2013-02-04 Fix to properly support accelerator pedals with only one potentiometer.
    [GEVCU.ino, pedal_pot.cpp]
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2013-02-11 Added provisions to support a setup routine for each device which is called automatically on start up
    Fixed some things which were preventing regen from working.
    Reworked throttle code heavily. It now will regen all of the way to the top of the pedal and won't fault unless the throttle goes a certain bit out of spec.
    [dmoc.cpp, motorctrl.cpp, pedal_pot.cpp]
2013-02-11 Fixed some mistakes that broke compiling.
    [motorctrl.cpp, pedal_pot.cpp]
2013-02-14 Reverse should now work.
    Added pretty well the rest of the 1.03 spec eeprom locations
    [dmoc.cpp, eeprom_layout.h]
2013-02-19 Implement proper state switching in DMOC code Started to add support for digital inputs to both throttle and motor controller Added a work in progress document with additional notes
    It compiles, I didn't test it (I'm sorry)
    [dmoc.cpp, motorctrl.cpp]
2013-02-20 Additional implementation of preference storage to EEPROM. Now both motor controller and pedal pot accelerator code will save/load parameters properly.
    Those parameters are now used by code so things are no longer hard coded.
    The start of some code to support both RPM and torque control in the DMOC
    The start of some implementation of support for brake pressure input.
    [GEVCU.ino, eeprom_layout.h, motorctrl.cpp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]
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2013-02-26 Fixed up an issue with not properly overloading the handleFrame function.
    [dmoc.cpp]
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2013-03-06 Some small mods. Doesn't compile. DOn't use it.
    [mem_cache.cpp]
2013-03-13 Added some explanation to the main file.
    Changed the name of some of my custom libraries to not
    conflict with the names of the official libraries.
    Fixed up the memcache code a bit.
    Added many more EEPROM locations for calibration,
    various baud rates, and other system settings.
    [GEVCU.ino, eeprom_layout.h, mem_cache.cpp]
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2013-03-20 Switch to using SerialUSB instead of Serial
    Changed all references to Serial to SerialUSB so that all debugging output
    runs over the normal USB connector instead of the debug connector. Why?
    Because connecting a PC to Serial reboots the Due. This is bad when you need
    the Due to be processing canbus frames for the DMOC. So, this change
    allows the Due to operate unimpeded. It also means you won't see the
    initial debugging output unless you push reset yourself.
    [GEVCU.ino]
2013-03-20 Fixed come errors that caused the sketch to not compile.
    Whoops...
    [mem_cache.cpp]
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2013-03-21 Added back in the preference saving/loading system
    Added back the code that was previously removed (in error)
    from the project. Also modified it to work with the caching system.
    [motorctrl.cpp]
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2013-03-24 Added missing digital input tests
    [GEVCU.ino]
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2013-03-26 Some fixes to TWI access to hopefully make it work better
    [mem_cache.cpp]
2013-04-21 Fixed a dumb transposition mistake that caused the detection of the current op state to fail and thus knocked out much of the DMOC functionality.
    Added the ability to track the actual gear being reported by the DMOC.
    [dmoc.cpp]
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2013-04-23 Some fixes to make the code compile. Whoops...
    [dmoc.cpp, ichip_2128.cpp]
2013-04-23 Mostly just switched back to USB output for the serial - Also small fix
    Fixed it up so DMOC is set to RPM mode when not using throttle.
    [GEVCU.ino]
2013-04-23 Fixed up some coding errors.
    Ramp testing will now work
    There is no longer any need to manually switch disabled->standby->enabled. Just plain select enabled and it will transition state.
    [dmoc.cpp]
2013-04-24 fixed a few glitches to get it compiling
    [GEVCU.ino, dmoc.cpp, ichip_2128.cpp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]
2013-04-26 Behold! A Visual Studio 2012 project for GEVCU.
    No, this doesn't mean you can compile the firmware in VS2012 but you can view it and edit it there. Here is what you want to do: Edit with VS2012 if that's your thing. Then, in the Arduino IDE File->Preferences->Use External Editor. Now you can edit with the external editor of choice and compile/upload with the Arduino IDE. It will all magically work. You're welcome for not having to use the craptastic Arduino IDE anymore.
    [GEVCU.sdf]
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2013-04-28 fixed minor glitch to get the LCD stuff compiling if desired.
    [GEVCU.ino]
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2013-04-29 Extra comments in code and implementation of automatic op/gear state in DMOC
    The DMOC code now automatically sets enabled op state when you try to go into gear. No more having to manually do this. Also, it won't actually shift into gear until the op state is enabled. This should make things completely automatic except that you still have to specify whether to go forward or backward.
    [dmoc.cpp, pedal_pot.cpp]
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2013-05-05 Added initialization code for sys params, fixed up sys_io a bit.
    [GEVCU.ino]
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2013-05-08 Add blinken lights, loosen throttle tolerance, change throttle defaults to be Due appropriate.
    [GEVCU.ino, config.h, pedal_pot.cpp]
2013-05-08 Fixes to allow use of VCU without a computer
    [GEVCU.ino]
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2013-05-08 Fixes to make system startup time drop from 3 seconds down to 16ms. MUCH BETTER!
    [GEVCU.ino, motorctrl.cpp]
2013-05-08 More fixes for quick start up and ability to disable drive
    Additional calls to handleTick to make sure DMOC stays active
    Disable the DMOC if the drive enable switch is not on.
    [GEVCU.ino]
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2013-05-11 Fixed up and enabled brake transducer code, Added debugging lines
    Fixed up the code for accelerator pedal and brake transducer tracking. It tests to work properly now for both.
    Added some additional comments
    Added some lines (commented out) for debugging
    Switched to default to single input throttle since I think the upcoming test will use only one pot.
    [GEVCU.ino, pedal_pot.cpp]
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2013-05-20 Fixed a couple of errors in the schematic
    Placed all parts on board approximately where they'll end up
    (in theory)
    [Eagle_Dued.brd, Eagle_Dued.sch]
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2013-05-29 Added analog shield, flipped Due on Dued board, fixed miniwifi footprint
    Added an analog shield that will be used for all analog input instead of placing it on the main DueD board. Also, now all boards will be two layer instead of four.
    Flipped over the Due on the DueD board. Now the DueD board is to have pins that stick up for the Due to
    mate to.
    Drastically improved the accuracy of the miniwifi layout.
    [Analog_Shield.brd, Analog_Shield.sch, Eagle_Dued.sch]
2013-06-01 Major redesign of board to encompass the entirety of the case we'd like to use.
    [Eagle_Dued.brd, Eagle_Dued.sch]
2013-06-03 Updated canbus board to be more correct, fixed size of ampseal connector, totally new DueD board.
    [Canbus-proto2.brd, Eagle_Dued.brd, Eagle_Dued.sch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]
2013-06-10 Additional corrections and goodness for the shields.
    [Canbus-proto2.brd, Eagle_Dued.brd, Eagle_Dued.sch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]
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2013-07-09 Updated canbus board to fix a layout issue, updated DueD to use DC/DC converter
    [Canbus-proto2.brd, Eagle_Dued.brd, Eagle_Dued.sch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]
2013-07-11 removed machina specific code, removed lcd implementation, fixed upper/lowercase of class names, variables and enums. started modification of CANHandler to support both can buses and allow devices to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
    [GEVCU.ino, config.h, dmoc.cpp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]
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2013-07-19 Canbus was being improperly initialized. This is now corrected.
    [GEVCU.ino]
2013-07-19 Additional comments, addition of raw adc mode
    Raw ADC mode allows for use of this code without the "proper" analog board. The analog board has differential output and so uses 8 ADC inputs for 4 actual inputs. Setting RAWADC reverts all the fancy stuff and gives you access to the normal Arduino ADC readings.
    [GEVCU.ino, config.h]
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2013-07-23 Slight fix to re-enable throttle debugging... sort of.
    [Heartbeat.cpp]
2013-07-23 Added more debugging output, added more comments, fixed sys_io preference reading, added sys_io_adc_poll back to loop.
    [GEVCU.ino, config.h]
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2013-07-26 fix bug with brake pedal
    [DeviceManager.cpp]
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2013-07-28 reduce coupling of canhandler, fix bug in DevMgr
    [DeviceManager.cpp]
2013-07-28 Fixed up GEVCU.ino file to make changes from Michael and Charles coexist.
    [GEVCU.ino]
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2013-07-29 Fix remaining copyright statements
    [DeviceManager.cpp, DmocMotorController.cpp, Heartbeat.cpp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]
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2013-08-01 Fixed code to compile once again
    There was an issue with improper case of an included header
    Code from cgalpin caused a minor issue in that DMOC code
    doesn't have access to runThrottle any longer. I don't
    think it's necessary is it? We'll see. Commented out.
    [DmocMotorController.cpp]
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2013-08-01 Correct improper mask in DMOC canbus listener setup, added conditional to allow compiling without the queue system, made buffer head/tail volatile.
    [DmocMotorController.cpp, GEVCU.ino]
2013-08-01 Fixes to allow use of code without the newest DueD board, read calibration data from EEPROM.
    [config.h]
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2013-08-02 More work on iChip2128.
    Don't worry, it doesn't mess anything up the way it is committed right
    now
    [ichip_2128.cpp]
2013-08-02 Make logger show throttle position, fix up saving of calibration
    [Heartbeat.cpp]
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2013-08-05 Slight simplification of DMOC loop, attempt to fix serial loop for iCHIP wifi
    [DmocMotorController.cpp, ichip_2128.cpp]
2013-08-08 Disable brake transducer code because it isn't set up properly yet. Change some accumulator variables to 32 bit to prevent overflows.
    [config.h]
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2013-08-13 Fixed up some merge errors that killed compile. Added hard coded mode
    Now you can set a flag to have it read parameters from Params.h instead of trying to use EEPROM. This should be easier during testing.
    Also fixed some spots were the merge went wonky and wrong code was left behind. It compiles now.
    Lastly, some cosmetic fix up where lines were reformatted to use tabs and be properly indented.
    [DmocMotorController.cpp, GEVCU.ino, MotorController.cpp]
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2013-08-19 re-enable tickHandler/timer queueing, works now
    With latest version of due_can.cpp, the Due no longer locks-up when
    processing tick-events in the main loop() and not within the interrupt.
    [DmocMotorController.cpp, config.h]
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2013-09-02 Fixed up brake calculations, fixed a problem with EEPROM storage for throttle params
    [Heartbeat.cpp, PotBrake.cpp, eeprom_layout.h]
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2013-09-03 Fixed improper line ending character. On accident it was hex 0x13 instead of decimal 13.
    [ichip_2128.cpp]
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2013-09-06 Fixed GEVCU.ino so that wifi stuff is only included if it is supposed to be.
    [GEVCU.ino]
2013-09-06 Add checks to new code in DeviceManager so that it doesn't try to access null pointers.
    [DeviceManager.cpp]
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2013-09-09 Proper fix for throttle pot issue kludged in last update.
    [config.h]
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2013-09-13 Fixes to allow for compiling while precharge code is written, change all variables in brake calc to be 32 bit.
    [GEVCU.ino, PotBrake.cpp, config.h]
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2013-09-16 Updated the build # and change log, some minor comment corrections
    [GEVCU.ino, config.h]
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2013-09-19 Allow DMOC to go by default. Fixed up some formatting, added more notes
    [DmocMotorController.cpp, GEVCU.ino, MotorController.cpp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]
2013-09-19 Implement (initial support) reverse limit, switch brake to using indep. min value, get existing values settable with serial console
    [GEVCU.ino, MotorController.cpp, MotorController.h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]
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2013-09-23 Fix to enable drive 2 seconds after ignition on to allow DMOC to come up first.
    [DmocMotorController.cpp]
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2013-09-25 Remove a todo from GEVCU.ino because it is done, fix size of canbus frames for think BMS keep alive.
    [GEVCU.ino]
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2013-09-26 Fixed oversights that caused the code to not compile properly.
    [DmocMotorController.cpp]
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2013-09-29 fixed rendering, display correct values in web page
    [BrusaMotorController.cpp, ichip_2128.cpp]
2013-09-30 Set pin 18 high for the GEVCU3 board to keep reset from being active.
    [ichip_2128.cpp]
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2013-10-01 Added console() method to Logger
    This method works like the other ones except will print at any log
    level and doesn't show the timestamp, devie id or log level. Applied
    it in a couple of places.
    [Heartbeat.cpp, MotorController.cpp]
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2013-10-08 minor fixes with calculation of values to display
    [ichip_2128.cpp]
2013-10-08 Fix to make auto transition to enabled/drive work properly
    [DmocMotorController.cpp]
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2013-10-16 New system in place which replaces the old #define system with EEPROM for device selection
    Now all devices are compiled into the firmware and can be selectively
    enabled and disabled in EEPROM. Except that there isn't any user
    facing way to do that right now.
    [BrusaMotorController.cpp, DmocMotorController.cpp]
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2013-10-16 Fixed up some merge problems to get things running again.
    [GEVCU.ino]
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2013-10-17 Various changes to further drive configuration to EEPROM instead of compile time constants.
    Now the board type can be specified on the serial console. It is respected and will be used to set up
    the system I/O. This pretty well brings the firmware to a point where EEPROM stores all the stuff we
    used to have to configure at compile time in order for everyone to build the copy they need. Now you just
    plain build and the EEPROM brings it all together.
    Note: EEPROM layout is different from how it was before this process started. Your settings *will* reset.
    Keep that in mind.
    [GEVCU.ino, config.h, eeprom_layout.h]
2013-10-17 Fixed operational glitches in the new device enable/disable system, added extra logging output
    This is now tested to work for enabling/disabling devices.
    [GEVCU.ino]
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2013-10-23 fixed logging of throttle errors, no regen ramp
    [PotBrake.cpp]
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2013-10-24 Fix to allow systype and log level to be set and persisted properly.
    [GEVCU.ino]
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2013-11-15 Added param caching to ichip
    Added param caching to the ichip class to reduce the amount of serial
    traffic to the ichip. Updates are now only made when needed and UI
    performance and stability seems to have improved.
    [ichip_2128.cpp]
2013-11-30 Proper two throttle pot support
    Made some changes to the throttle calibration to fix issues since
    refactoring. Also added output of percentage of fluctuation of pedal
    values at rest and full throttle during calibration.
    Changed the pot throttle to use a percentage threshold for validation
    and not raw values
    Implemented support for two throttles with the second inverted
    Increased the config thresholds for invalid values since I am getting
    in excess of 10% fluctuation in values
    [config.h]
2013-12-09 Added ability to scan for nearby access points
    Fixed setting of wifi type. You must DOWN the ichip module in order to set the type.
    [ichip_2128.cpp]
2013-12-16 Additional support for V4 boards
    A small addition to give an error if an invalid system type was specified on the console.
    [ichip_2128.cpp]
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2014-01-06 Updates to compile against newest canbus library
    The canbus library was changed to include more functionality, be easier to use,
    and generally be better. There are no longer RX and TX specifications for frames,
    just one type. Also, many other things that CanHandler did are now in the canbus
    library.
    [BrusaMotorController.cpp, CanPIDListener.cpp]
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2014-02-13 Sync with EVTV released code
    EVTV has released the first official version of the GEVCU code. The biggest differences from what existed here:
    1. Addition of cooling. The code can now turn on/off a cooling fan in response to motor controller / motor temperature
    2. Fixed the precharge for the motor controller
    3. Made the serial console look better.
    All changes in this commit were initially done by Jack Rickard of EVTV and merged into this code base by Collin Kidder. Blame me if they're broken now.
    [GEVCU.ino, Heartbeat.cpp, MotorController.cpp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]
2014-03-06 Fixed config.h to properly default to using SerialUSB. 95% of everyone is going to need that default now.
    [config.h]
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2014-03-19 Fixes to make the elm327 code compile. Also, integrated elm327 into the device manager and startup system so it is possible to enable and disable it now.
    [GEVCU.ino]
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2014-03-20 Fix a compile warning, fix output of OBD2 comm over ELM327 emulator with headers enabled.
    [OBD2Handler.cpp]
2014-03-24 Fixed bug in OBD2 - Code wasn't advertising two PIDs that we do in fact support.
    [OBD2Handler.cpp]
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2014-03-25 A whole lot of debugging output, Additional code to support talking to torque over wifi. Right now things are kind of broken if parameter polling is turned on. So, it's disabled. Don't run this. Just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
    [ichip_2128.cpp]
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2014-04-07 So, that last update that was supposed to make device init easy just broke everything. Here is try two. This one works, scout's honor.
    [BrusaMotorController.cpp, DeviceManager.cpp]
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2014-04-10 Fixed up some lingering problems with ichip code that caused things to be very brittle on startup and sometimes when running. It's not perfect yet but it operates properly under testing.
    [ichip_2128.cpp]
2014-07-03 Added CodaMotorController
    Does not seem to recognize as a motorcontroller. Alsmost as if it
    isn’t loading the parent configuration. for MotorController.
    Configuration parameters are not persistant across resets in teh EEPROM
    [CodaMotorController.cpp, GEVCU.ino, MotorController.h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]
2014-07-04 Fix to not return a disabled device from DeviceManager::getDeviceByType
    [DeviceManager.cpp]
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2014-07-04 Fixed Operating Time and Web Page Variable Display
    Web page would often not load until a change was made in serial port.
    Operating time was not displaying. Lots of little fixes.
    Changed torqueRequested in CodaMotorController to NOT include the
    offset. Need to do this in DMOC Motor Controller as well. This is
    because the offsets, which we were taking out in ICHIP are different
    between the two, and likely from one inverter to the next.
    [CodaMotorController.cpp, MotorController.cpp, MotorController.h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]
2014-07-05 Lots of MotorController
    Promoted Operation State (enable/disable) and gears (forward/reverse)
    to parent MotorController and eliminated them in childs DMOC645 and Coda
    added code for a reverse input that will put the device in reverse
    Added code for an enable input that can be used to put a device into
    disabled state
    added brakelight output to turn on brakelights during regen.
    added a reverse light output to activate reverse lights when were in
    reverse gear.
    [CodaMotorController.cpp, DmocMotorController.cpp, MotorController.cpp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]
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2014-07-07 Various ICHIP and CODA fixes
    Guarded throttle level so <-600 =600
    Attempted and failed to fix web site configuration which displays
    nonsense on a cold start.
    [CodaMotorController.cpp, GEVCU.ino, ichip_2128.cpp]
2014-07-09 Revised Max RPM use
    Max RPM on the config screen, as it turns out, was only used to set the
    speed command in the DMOC in speed mode.
    The web page implies we are setting a maximum RPM which will not be
    exceeded yet there is nothing in eithe CodaMotorController or
    DmocMotorController to implement this.
    Added code to send a ZERO torque command in the event the inverter
    reports an actual speed greater than the maximum rpm.
    This should prevent running the motor above max rpm.
    [CodaMotorController.cpp, DmocMotorController.cpp]
2014-08-19 It WORKS
    1.54 was the clue. Ran 35 minutes with no issues. Incorporates a
    REVERSE input and an ENABLE input.
    [CodaMotorController.cpp, GEVCU.ino, MotorController.cpp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]
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2014-08-23 REVERSE and ENABLE functions
    Added annunciators for digital inputs 0-3 and the ENABLE and REVERSE
    annunciators.
    [MotorController.cpp, MotorController.h]
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2014-09-02 Reimplemented some Coverity fixes from the ArduinoDue branch. Fixes up some small issues in the code.
    [CanPIDListener.cpp, MemCache.cpp, MotorController.cpp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]
2014-09-02 New Wireless Commands and Initialization
    1. Changed GEVCU.ino where initialization of WiReach chip only occurs
    if EEPROM init is run.
    2. Solved the longsuffering ongoing problem of ICHIP not loading
    parameters when the program first comes up. Added a loopcount variable
    to Serial Console. At loopcount == 10,000 it forces ICHIP to load
    parameters. The website now comes up wiht all parameters loaded -
    every time.
    3. Added WIREACH command. WIREACH=anycommand will send At+ianycommand
    to the wireless device.
    4. Added SSID command. SSID=whatevername will set the SSID of the
    wireless device to “whatevername”.
    Active immediately.
    5. Added IP command. IP=192.168.3.10 will change the curr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
    [GEVCU.ino, connectTOap.ino, connectasAP.ino]
2014-09-04 Wireless Channel and Security
    Added wireless initialization WSEC to select WPA2-AES as wireless
    security IF used.
    Added SECURITY command to set the WPA2 password and turn security on.
    SECURITY=password
    Added CHANNEL command to allow you to change the wireless channel used
    to avoid interference from other local broadcasts. CHANNEL=7
    [GEVCU.ino]
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2014-09-16 UQM Changes and Temperature Changes
    Altered calculations for DMOC temperatures and UQM torque. Checked
    ENABLE and REVERSE inputs on UQM
    [CodaMotorController.cpp, DmocMotorController.cpp, MultiSerial.ino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]
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2014-09-17 Changes to DMOC code to make it respect enable and reverse inputs.
    [DmocMotorController.cpp]
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2014-09-22 Fixed some bugs that prevented DMOC code from properly controlling the DMOC.
    [DmocMotorController.cpp, GEVCU.ino]
2014-09-23 Tested on DMOC Bench and THING
    Reverse works. Enable works. Tested on DMOC bench and on VW Thing.
    [CodaMotorController.cpp, DmocMotorController.cpp, MotorController.cpp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]
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2014-10-03 Add a new command to reset the EEPROM storage for every device: NUKE=1 use it sparingly.
    [GEVCU.ino]
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2015-03-15 Added EVIC Object Module
    Added EVIC Object Module to send CAN data to Andromeda Interfaces EVIC
    display system.
    Numerous other cleanups and fixes.
    [Analog_Board.brd, Analog_Board.sch, Analog_Shield.brd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]
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2015-09-27 Set digital outputs a lot sooner. This should fix the issue where relays were triggering for a short time before being properly set off.
    [GEVCU.ino]
2016-10-05 Fix some issues with DMOC code, removed regen when speed is low, reformatted "L" command output
    [DmocMotorController.cpp, Heartbeat.cpp]
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

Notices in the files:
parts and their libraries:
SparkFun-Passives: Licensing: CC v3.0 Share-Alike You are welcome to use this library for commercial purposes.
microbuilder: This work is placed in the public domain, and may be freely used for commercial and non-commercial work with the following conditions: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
